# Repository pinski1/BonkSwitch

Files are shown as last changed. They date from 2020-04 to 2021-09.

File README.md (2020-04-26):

# BonkSwitch
For the remote control of 2 solenoids.

<!-- 3D image of the board here -->

## Specification

* Will accept +30V (8s) to +52 (12s) input voltages on an XT60 connector
* Will drive 2 solenoids with +24V at 60W each via XT30 connectors.
* Has an on board [FrSky XM](https://www.frsky-rc.com/product/xm-1g-sbus-non-telemetry/) reciever with 15 channels
* Will accept any [Adafruit Feather](https://learn.adafruit.com/adafruit-feather/feather-specification) compatible microcontroller board.
* Has voltage monitoring of all power rails and current monitoring of solenoids

While example code is provided it will require modification for your application & chosen Feather.

## Current status

Currently the PCB is in the final stages of review and should be finalised shortly.

The firmware efforts are still on going, although the majority of the work can only be completed once the hardware is available.

## Acknowledgements

* The team behind the robot [Nelly the Ellybot](https://www.facebook.com/teampunchant/)
* The team at [Bristol Bots](https://bristolbotbuilders.com/)
* My friend [Steve](https://twitter.com/BookSwapSteve) for the Feather outline

## Licence
Don't be a tit.
But see LICENCE for more details/legalese.

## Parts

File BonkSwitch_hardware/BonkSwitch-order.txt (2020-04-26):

Quantity	Value	Package	Order code	Manufacturer	Manuf. Code	Availability	Price (from)	Description
1	FEATHERWING_NODIM	FEATHERWING_DIM	unknown					
1	FRSKY_XM+	FRSKY_XM+	unknown					
10	100nF	C0603	unknown					
4	2.2uF 100V	C1210	2112727	TDK	C3225X7R2A225K230AB	10989	0.129	TDK - C3225X7R2A225K230AB - SMD Multilayer Ceramic Capacitor, 2.2 µF, 100 V, 1210 [3225 Metric], ± 10%, X7R, C Series TDK
4	10nF	C0603	unknown					
2	10uF 35V	C1210	2309017	TAIYO YUDEN	GMK325AB7106MM-T	1980	0.144	TAIYO YUDEN - GMK325AB7106MM-T - SMD Multilayer Ceramic Capacitor, 10 µF, 35 V, 1210 [3225 Metric], ± 20%, X7R, M Series
1	470pF	C0603	unknown					
1	100pF	C0603	unknown					
1	1uF	C0805	unknown					
1	47uF 100V	UD-10X10_NICHICON	1973389	PANASONIC	EEEHA2A470UP	1524	0.337	PANASONIC - EEEHA2A470UP - SMD Aluminium Electrolytic Capacitor, Radial Can - SMD, 47 µF, 100 V, HA Series, 1000 hours @ 105°C
1	120uF 35V	PANASONIC_E	2354806	PANASONIC	35SVPF120M	1	0.773	PANASONIC - 35SVPF120M - Polymer Aluminium Electrolytic Capacitor, 120 µF, 35 V, Radial Can - SMD, OS-CON SVPF Series
2	5.6V	SOD-323	unknown					
4	PMEG10030ELPX	SOD128	2498548	NEXPERIA	PMEG10030ELPX	52918	0.0919	NEXPERIA - PMEG10030ELPX - Schottky Rectifier, 100 V, 3 A, Single, SOD-128, 2 Pins, 770 mV
1	MBR130	SOD-123	2463407	ON SEMICONDUCTOR	MBR130LSFT1G	5080	0.0611	ON SEMICONDUCTOR - MBR130LSFT1G - Schottky Rectifier, 30 V, 1 A, Single, SOD-123FL, 2 Pins, 380 mV
1	LMR16030SDDAR	HSOIC8	2617078	TEXAS INSTRUMENTS	LMR16030SDDA .	637	1.96	TEXAS INSTRUMENTS - LMR16030SDDA . - DC/DC Switching Buck Regulator, Adjustable, 4.3V-60V in, 0.8V-50V out, 3A, HSOIC-8
1	LMR16006XDDC	SOT23-6	3007251	TEXAS INSTRUMENTS	LMR16006XDDCR	6791	1.13	TEXAS INSTRUMENTS - LMR16006XDDCR - DC-DC Switching Buck Step Down Regulator, Adjustable, 4V-60Vin, 2.1 MHz, 0.8V-55V/0.6Aout, SOT-6
1	FAN3227TMX	SOIC127P600X175-8N	2563218	ON SEMICONDUCTOR	FAN3227TMX	1885	0.437	ON SEMICONDUCTOR - FAN3227TMX - MOSFET Driver, 4.5V-18V supply, 3A output, SOIC-8
2	LMP8640MK-T	SOT23-6	3005385	TEXAS INSTRUMENTS	LMP8640MK-T/NOPB	0	0.676	TEXAS INSTRUMENTS - LMP8640MK-T/NOPB - Current Sense Amplifier, 1 Amplifier, 13 µA, TSOT-23, 6 Pins, -40 °C, 125 °C
1	74LVC1G14DBV	SOT23-5	1631687	NEXPERIA	74LVC1G14GW,125	14643	0.0387	NEXPERIA - 74LVC1G14GW,125 - Inverter, Schmitt Trigger, 74LVC1G14, 1 Input, 50 mA, 1.65 V to 5.5 V, TSSOP-5
1	7443551221	WE-HCI_1350/1365	2082647	WURTH ELEKTRONIK	7443551221	310	2.48	WURTH ELEKTRONIK - 7443551221 - Power Inductor (SMD), 22 µH, 6 A, Shielded, 6.5 A, WE-HCI Series, 13.2mm x 12.8mm x 6.2mm
1	7447714470	WE-PD_1030/1050	2082682	WURTH ELEKTRONIK	7447714470	1457	1.55	WURTH ELEKTRONIK - 7447714470 - Power Inductor (SMD), 47 µH, 2.2 A, Shielded, 2.5 A, WE-PD Series, 10mm x 10mm x 5mm
2	GREEN	LED-0603	unknown					
1	RED	LED-0603	unknown					
2	Yellow	LED-0603	unknown					
1	PCB_DP_RECTANGLE-100X62	DP10062_V1	unknown					
1	SI2302CDS	SOT23	1684049	VISHAY	SI2302CDS-T1-GE3	8121	0.13	VISHAY - SI2302CDS-T1-GE3 - Power MOSFET, N Channel, 20 V, 2.9 A, 0.045 ohm, TO-236, Surface Mount
4	2k2	R0603	unknown					
2	0R01	R2512	1435947	BOURNS	CRA2512-FZ-R010ELF	14930	0.208	BOURNS - CRA2512-FZ-R010ELF - SMD Current Sense Resistor, 0.01 ohm, CR Series, 2512 [6432 Metric], 3 W, ± 1%, Metal Film
2	10R	R0805	unknown					
2	39k	R0805	unknown					
1	82k	R0603	unknown					
2	470k	R0603	unknown					
1	33k	R0603	unknown					
1	30k	R0603	unknown					
1	4k3	R0603	unknown					
2	47k	R0603	unknown					
1	130k	R0603	unknown					
2	20k	R0603	unknown					
1	620k	R0603	unknown					
1	2k2	R0805	unknown					
1	56k	R0603	unknown					
1	68k	R0603	unknown					
1	11k	R0603	unknown					
4	100R	R0603	unknown					
5	10k	R0603	unknown					
4	SHORTT1	SHORT_TOP-01	unknown					
2	IRF7493TRPBF	SO-08	2725911	INFINEON	IRF7493TRPBF	4215	0.42	INFINEON - IRF7493TRPBF - Power MOSFET, N Channel, 80 V, 9.3 A, 0.0115 ohm, SOIC, Surface Mount
3	TESTPOINT_1.5X1.5	TESTPAD_1.5X1.5	unknown					
1	XT60PW-M	XT60PW-M	unknown					
2	XT30PW-F	XT30PW-F	unknown

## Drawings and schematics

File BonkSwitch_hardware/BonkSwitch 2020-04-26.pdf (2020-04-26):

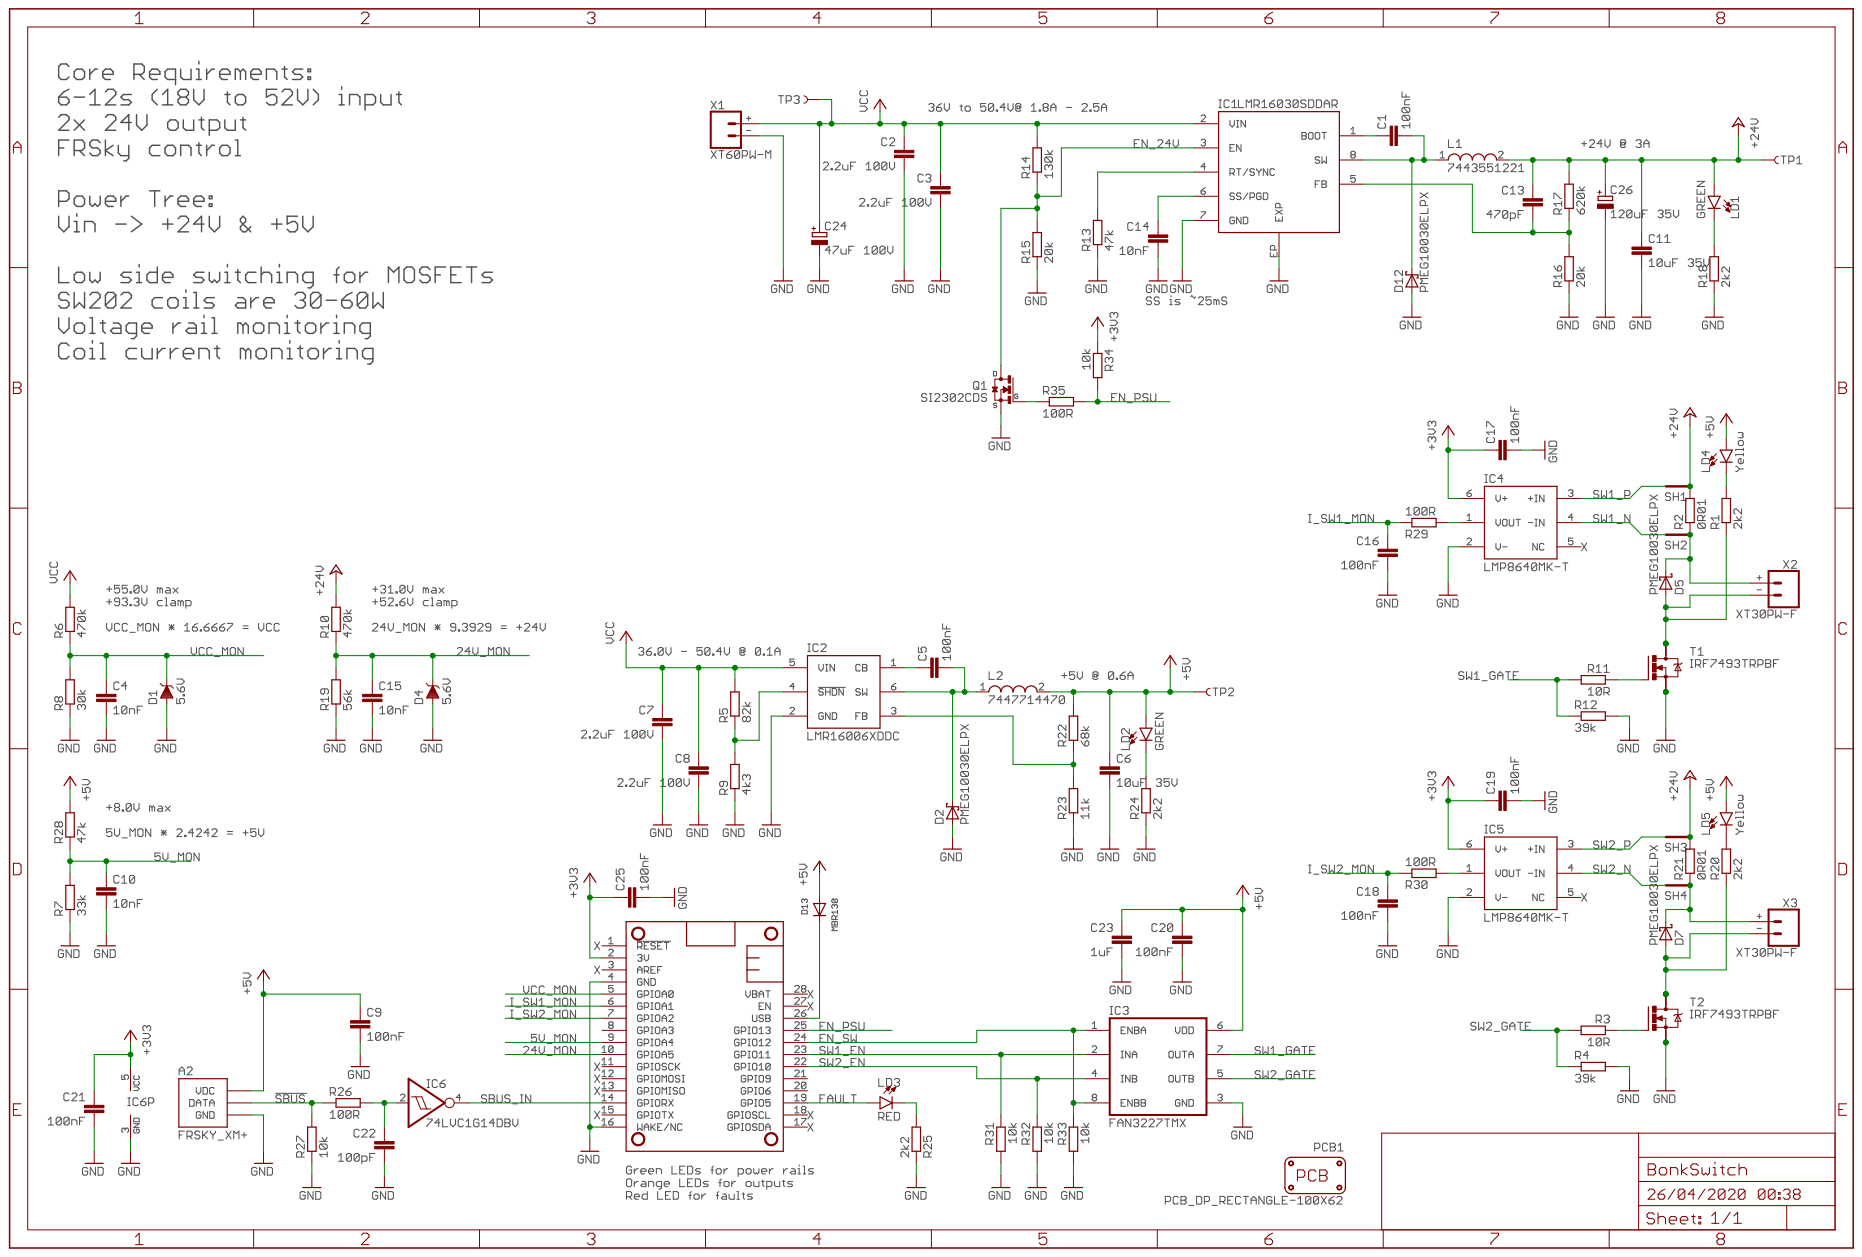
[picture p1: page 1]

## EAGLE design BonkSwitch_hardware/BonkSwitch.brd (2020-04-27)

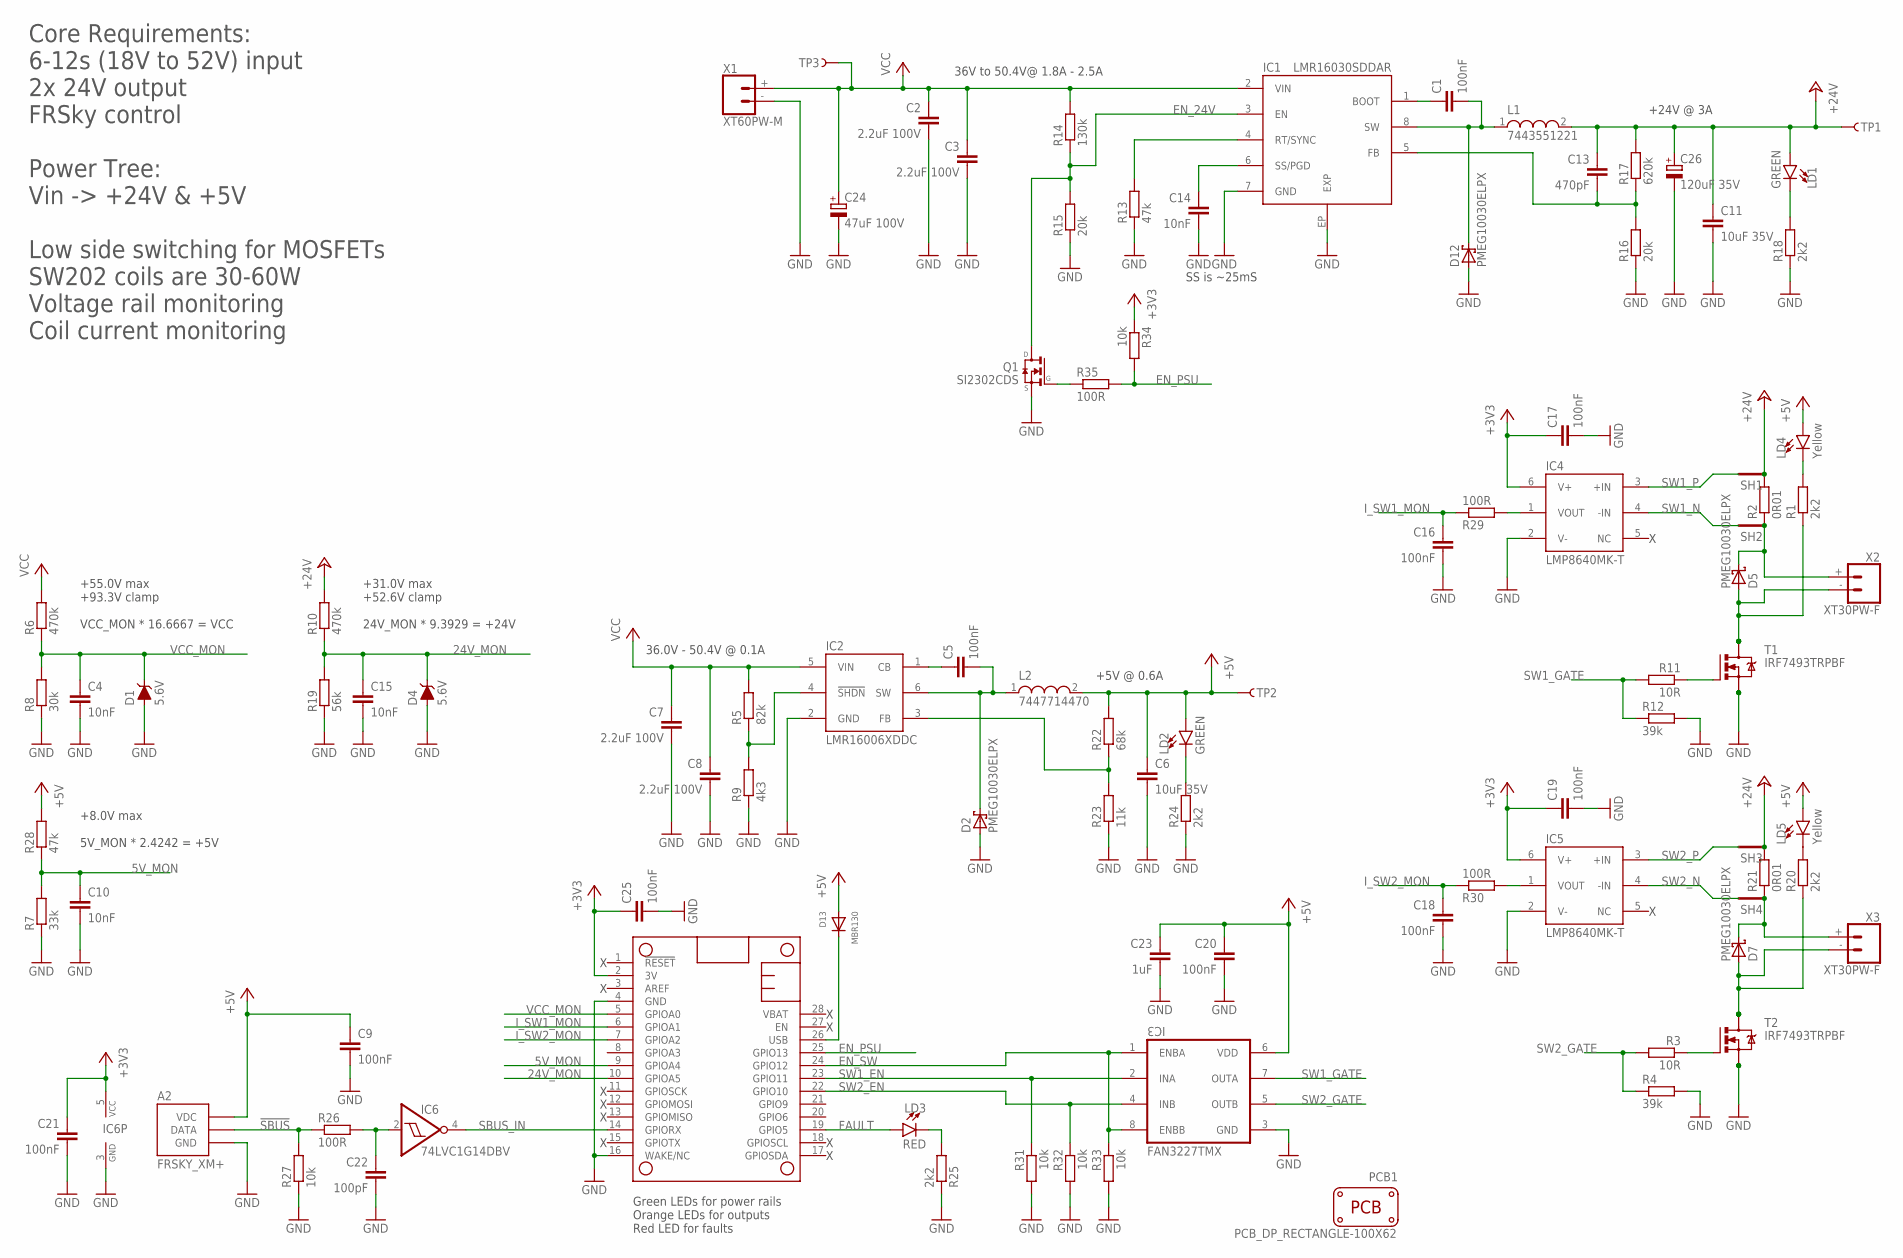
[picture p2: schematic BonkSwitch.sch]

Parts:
A1: FEATHERWING_NODIM; FEATHERWING_DIM
A2: FRSKY_XM+
C1, C5, C9, C16, C17, C18, C19, C20, C21, C25: 100nF; C0603
C2, C3, C7, C8: 2.2uF 100V; C1210; MPN C3225X7R2A225K230AB
C4, C10, C14, C15: 10nF; C0603
C6, C11: 10uF 35V; C1210; MPN GMK325AB7106MM-T
C13: 470pF; C0603
C22: 100pF; C0603
C23: 1uF; C0805
C24: 47uF 100V; UD-10X10_NICHICON; MPN EEEHA2A470UP
C26: 120uF 35V; PANASONIC_E; MPN 35SVPF120M
D1, D4: 5.6V; SOD-323; MPN MM3Z4V3ST1G
D2, D5, D7, D12: PMEG10030ELPX; SOD128; MPN PMEG10030ELPX
D13: MBR130; SOD-123; MPN MBR130LSFT1G
IC1: LMR16030SDDAR; HSOIC8; MPN LMR16030SDDA .
IC2: LMR16006XDDC; SOT23-6; MPN LMR16006XDDCR
IC3: FAN3227TMX; SOIC127P600X175-8N; MPN FAN3227TMX
IC4, IC5: LMP8640MK-T; SOT23-6; MPN LMP8640MK-T/NOPB
IC6: 74LVC1G14DBV; SOT23-5; MPN 74LVC1G14GW,125
L1: 7443551221; WE-HCI_1350/1365; MPN 7443551221
L2: 7447714470; WE-PD_1030/1050; MPN 7447714470
LD1, LD2: GREEN; LED-0603
LD3: RED; LED-0603
LD4, LD5: Yellow; LED-0603
PCB1: PCB_DP_RECTANGLE-100X62; DP10062_V1
Q1: SI2302CDS; SOT23; MPN SI2302CDS-T1-GE3
R1, R20, R24, R25: 2k2; R0603
R2, R21: 0R01; R2512; MPN CRA2512-FZ-R010ELF
R3, R11: 10R; R0805
R4, R12: 39k; R0805
R5: 82k; R0603
R6, R10: 470k; R0603
R7: 33k; R0603
R8: 30k; R0603
R9: 4k3; R0603
R13, R28: 47k; R0603
R14: 130k; R0603
R15, R16: 20k; R0603
R17: 620k; R0603
R18: 2k2; R0805
R19: 56k; R0603
R22: 68k; R0603
R23: 11k; R0603
R26, R29, R30, R35: 100R; R0603
R27, R31, R32, R33, R34: 10k; R0603
SH1, SH2, SH3, SH4: SHORTT1; SHORT_TOP-01
T1, T2: IRF7493TRPBF; SO-08; MPN IRF7493TRPBF
TP1, TP2, TP3: TESTPOINT_1.5X1.5; TESTPAD_1.5X1.5
X1: XT60PW-M
X2, X3: XT30PW-F

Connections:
5V_MON: A1.9 (GPIOA4), C10.1, R7.2, R28.1
24V_MON: A1.10 (GPIOA5), C15.1, D4.C, R10.1, R19.2
!SBUS: A2.3 (DATA), R26.1, R27.2
!SBUS_FILT: C22.1, IC6.2 (I), R26.2
+3V3: A1.2 (3V), C17.1, C19.1, C21.1, C25.1, IC4.6 (V+), IC5.6 (V+), IC6.5 (VCC), R34.1
+5V: A2.2 (VDC), C6.1, C9.1, C20.1, C23.1, D13.A, IC3.6 (VDD), L2.2, LD2.A, LD4.A, LD5.A, R22.2, R28.2, TP2.1
+24V: C11.1, C13.1, C26.+, L1.2, LD1.A, R2.2, R10.2, R17.2, R21.2, SH1.1, SH3.1, TP1.1
BST_5V: C5.1, IC2.1 (CB)
BST_24V: C1.1, IC1.1 (BOOT)
EN_5V: IC2.4 (!SHDN!), R5.1, R9.2
EN_24V: IC1.3 (EN), Q1.3 (D), R14.1, R15.2
EN_PSU: A1.25 (GPIO13), R34.2, R35.2
EN_SW: A1.24 (GPIO12), IC3.1 (ENBA), IC3.8 (ENBB), R33.1
FAULT: A1.19 (GPIO5), LD3.A
FB_5V: IC2.3 (FB), R22.1, R23.2
FB_24V: C13.2, IC1.5 (FB), R16.2, R17.1
GND: A1.4 (GND), A1.16 (WAKE/NC), A2.1 (GND), C2.2, C3.2, C4.2, C6.2, C7.2, C8.2, C9.2, C10.2, C11.2, C14.2, C15.2, C16.2, C17.2, C18.2, C19.2, C20.2, C21.2, C22.2, C23.2, C24.-, C25.2, C26.-, D1.A, D2.A, D4.A, D12.A, IC1.7 (GND), IC1.EP (EXP), IC2.2 (GND), IC3.3 (GND), IC4.2 (V-), IC5.2 (V-), IC6.3 (GND), Q1.2 (S), R4.2, R7.1, R8.1, R9.1, R12.2, R13.1, R15.1, R16.1, R18.1, R19.1, R23.1, R24.1, R25.1, R27.1, R31.2, R32.2, R33.2, T1.1 (S), T1.2 (S), T1.3 (S), T2.1 (S), T2.2 (S), T2.3 (S), X1.- (1)
I_SW1: IC4.1 (VOUT), R29.2
I_SW1_MON: A1.6 (GPIOA1), C16.1, R29.1
I_SW2: IC5.1 (VOUT), R30.2
I_SW2_MON: A1.7 (GPIOA2), C18.1, R30.1
unnamed: D7.C, R21.1, SH4.1, X3.+ (2)
unnamed: Q1.1 (G), R35.1
unnamed: R11.1, T1.4 (G)
unnamed: D5.A, R1.1, T1.5 (D), T1.6 (D), T1.7 (D), T1.8 (D), X2.- (1)
unnamed: LD4.C, R1.2
unnamed: R3.1, T2.4 (G)
unnamed: D7.A, R20.1, T2.5 (D), T2.6 (D), T2.7 (D), T2.8 (D), X3.- (1)
unnamed: LD5.C, R20.2
unnamed: D5.C, R2.1, SH2.1, X2.+ (2)
unnamed: LD3.C, R25.2
unnamed: LD1.C, R18.2
unnamed: LD2.C, R24.2
RT_24V: IC1.4 (RT/SYNC), R13.2
SBUS_IN: A1.14 (GPIORX), IC6.4 (O)
SS_24V: C14.1, IC1.6 (SS/PGD)
SW1_EN: A1.23 (GPIO11), IC3.2 (INA), R31.1
SW1_GATE: IC3.7 (OUTA), R11.2, R12.1
SW1_N: IC4.4 (-IN), SH2.2
SW1_P: IC4.3 (+IN), SH1.2
SW2_EN: A1.22 (GPIO10), IC3.4 (INB), R32.1
SW2_GATE: IC3.5 (OUTB), R3.2, R4.1
SW2_N: IC5.4 (-IN), SH4.2
SW2_P: IC5.3 (+IN), SH3.2
SW_5V: C5.2, D2.C, IC2.6 (SW), L2.1
SW_24V: C1.2, D12.C, IC1.8 (SW), L1.1
VCC: C2.1, C3.1, C7.1, C8.1, C24.+, IC1.2 (VIN), IC2.5 (VIN), R5.2, R6.2, R14.2, TP3.1, X1.+ (2)
VCC_MON: A1.5 (GPIOA0), C4.1, D1.C, R6.1, R8.2
V_USB: A1.26 (USB), D13.C

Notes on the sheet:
Core Requirements: 6-12s (18V to 52V) input 2x 24V output FRSky control Power Tree: Vin -> +24V & +5V Low side switching for MOSFETs SW202 coils are 30-60W Voltage rail monitoring Coil current monitoring
+55.0V max +93.3V clamp VCC_MON * 16.6667 = VCC
+31.0V max +52.6V clamp 24V_MON * 9.3929 = +24V
+24V @ 3A
36V to 50.4V@ 1.8A - 2.5A
+5V @ 0.6A
36.0V - 50.4V @ 0.1A
Green LEDs for power rails Orange LEDs for outputs Red LED for faults
SS is ~25mS
+8.0V max 5V_MON * 2.4242 = +5V

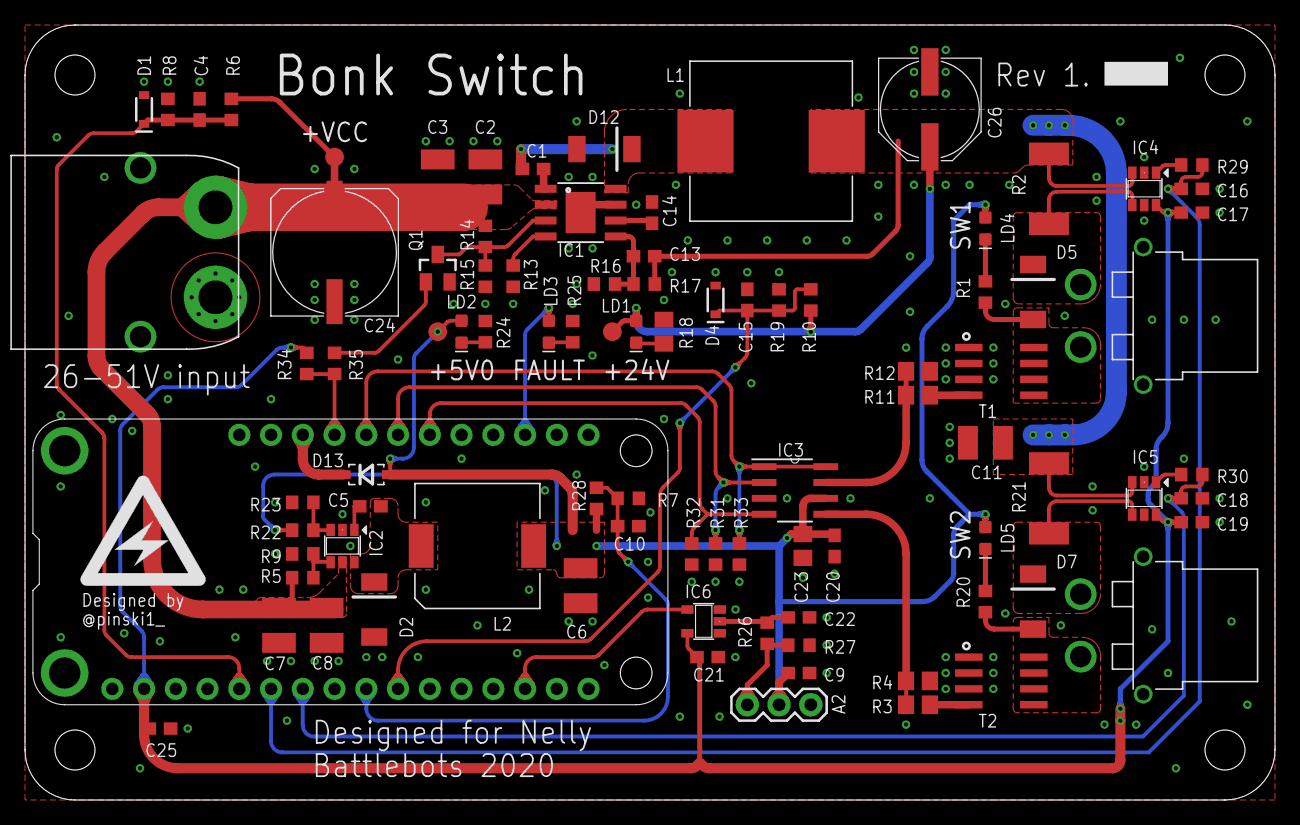
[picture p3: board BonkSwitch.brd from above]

Board: 2 copper layers, 100.0 x 62.0 mm, 97 parts (0 on the bottom side), 49 nets.

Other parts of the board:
LG1: LOGO_10X10

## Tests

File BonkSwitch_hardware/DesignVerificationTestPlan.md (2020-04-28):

# Bonk Switch - Design Verification Test Plan
Need to test the design to verify it meets the specification.

## Equipment Required

|Equipment|Model|Serial Number|
|---|-----|---|
|PSU, 60V 3A|||
|XT60 cable|||
|XT30 10Ω load|||
|Multi-meter|||
|Oscilloscope|||
|Oscilloscope probes|||
|USB Micro cable|||
|Thermal Camera|||

## Test Plan

|Test|Description|Criteria|Pass |Notes|
|----|---|---|-----|-----|
|Visually inspect the board|Is anything out of place?|Shorts|❌| |
|||Tombstoning|❌| |
|||PCB Faults|❌| |
|||Cold joints|❌| |
|||Serial Number present|❌| |
|Test for Shorts|Multi-meter on conitinuity mode||
|||OC between VCC (TP3) & GND|❌| |
|||OC between +24V (TP1) & GND|❌| |
|||OC between +5V (TP2) & GND|❌| |
|||OC between +3V3 (A1.p2) & GND|❌| |

Remove the Feather for the following tests.

Apply current limited +40V @ 3A power via the XT60.

|Test|Description|Criteria|Pass |Notes|
|----|---|---|-----|-----|
| | | |❌| |
|Measure the voltage|VCC (TP3) & GND |VCC ±5%|❌| |
||+5V (TP2) & GND|+4.75V & +5.25V|❌| |
||+24V (TP1) & GND|0V & +0.08V|❌| |
|Check LEDs|+5V LED (LD2)|lit|❌| |
||+24V LED (LD1)|unlit|❌| |
||Fault LED (LD3)|unlit|❌| |
||SW1 LED (LD4)|unlit|❌| |
||SW2 LED (LD5)|unlit|❌| |

Place a jumper between pin 25 and pin 4 on the Feather to enable the +24V SMPS.

|Test|Description|Criteria|Pass |Notes|
|----|---|---|-----|-----|
|Measure the voltage|+24V (TP1) & GND |+21.60V & +26.40V|❌| |
|Check LEDs|+24V LED (LD1)|lit|❌| |
|Check Board Temp|Use thermal camera|No hot spots|❌| |

Remove power to board and jumper wire.

Program Feather with bringup firmware.

Fit Feather to board.

Apply current limited +40V @ 3A power via the XT60.

|Test|Description|Criteria|Pass |Notes|
|----|---|---|-----|-----|
|Feather powered|Check LEDs on feather|lit|❌| |
|Feather communicating|Plug USB cable in|Characters on terminal|❌| |
|ADC reading correctly|VCC_MON|raw: xxxx to xxxx|❌| |
||+5V_MON|raw: xxxx to xxxx|❌| |
|Feather controls +24V|Enable +24V SMPS|TP1 +21.60V & +26.40V|❌| |
|Check LEDs|Fault LED (LD3)|lit|❌| |
|ADC reading correctly|+24V_MON|raw: xxx to xxx|❌| |

* MOSFET switch testing
   * check MOSFETs are driven on with minimal ringing
   * check MOSFET on resistance is reasonable
   * check SW1 is feather controlled
   * check SW2 is feather controlled
   * check against load of 10Ω
||I_SW1_MON|raw: 0 to xxxx|❌| |
||I_SW2_MON|raw: 0 to xxxx|❌| |

* FrSky RX testing
   * recieving FrSky packets
   * able to bind FrSky to RX
   * can see sticks moving
* confirm operation when VCC >50V and <35V

## Test Conclusion

1. Fault with design
   1. PCB mod
   2. PCB fix

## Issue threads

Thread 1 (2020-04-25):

Need to move +5V monitoring off of A9

pinski1, 2020-04-25:
A9 isn't compiling correctly in the Arduino IDE. The pin also shares a 100k to the on board battery connection so may be pulled to +4.2V by the Lithium battery charger.

This will also allow the potential divider to be set to something a little more reasonable than 2x 100kΩ resistors. Use [this](http://www.ti.com/download/kbase/volt/volt_div3.htm) to calculate the new resistor values. Bonus points if it's an integer conversion factor.

pinski1, 2020-04-25:
Moved to A4.
Resistor divider made up of 47kΩ and 33kΩ.
Fixed in commit fd1ea05e47847317a846a86c4f4bd8a77284a996

Closed 2020-04-25.

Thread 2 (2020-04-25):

Missing a Bill of Materials

pinski1, 2020-04-25:
A basic BoM needs to be generated and uploaded.

pinski1, 2020-04-26:
Added in f1a38f9bac2f6656c8cff0e34b6bc3c29929b90a

Closed 2020-04-26.

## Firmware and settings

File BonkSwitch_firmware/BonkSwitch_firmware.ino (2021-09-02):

/** BonkSwitch
 *
 * See https://www.ti.com/tool/TIDA-00289
 *
 *
 * Written for the [Adafruit Feather M0 Basic Proto](https://www.adafruit.com/product/2772)
 * Using https://github.com/bolderflight/SBUS
 */
#include <elapsedMillis.h>
#include <SBUS.h>

/** Settings **/
const unsigned int loop_duration_us = 10000; // 100Hz → 10ms
// forward duration
// return duration
// RC channel settings


/** Pin Map **/
#define PIN_VCC_MON       (A0)
#define PIN_24V_MON       (A5)
#define PIN_5V_MON        (A4)
#define PIN_I_SW1_MON     (A1)
#define PIN_I_SW2_MON     (A2)
#define PIN_EN_PSU        (13)  // active low
#define PIN_EN_SW         (12)
#define PIN_SW1_EN        (11)
#define PIN_SW2_EN        (10)
#define PIN_FAULT         (5)
#define PIN_SBUS_IN       (0)

/** Prototypes **/
unsigned int convert_ADC(int channel);
SBUS rc_rx(Serial1);
elapsedMicros loop_elapsed_us;

/** Globals **/
enum _states {s_Failsafe, s_Idle, s_Firing, s_Returning} current_state;
volatile unsigned int counter_packet_missed = 0x00;
bool flag_packet_rdy;
uint16_t channels[16];
bool failSafe;
bool lostFrame;
unsigned int mon_vcc;
unsigned int mon_24v;
unsigned int mon_5v;
unsigned int mon_sw1;
unsigned int mon_sw2;
unsigned int eqv_12v;
unsigned int coil_current[2][20];
unsigned int coil_curr_index = 0;
String debug_buffer;


void setup(void) {

  pinMode(PIN_VCC_MON, INPUT);
  pinMode(PIN_24V_MON, INPUT);
  pinMode(PIN_5V_MON, INPUT);
  pinMode(PIN_I_SW1_MON, INPUT);
  pinMode(PIN_I_SW2_MON, INPUT);
  pinMode(PIN_EN_PSU, OUTPUT);
  pinMode(PIN_EN_SW, OUTPUT);
  pinMode(PIN_SW1_EN, OUTPUT);
  pinMode(PIN_SW2_EN, OUTPUT);
  pinMode(PIN_FAULT, OUTPUT);

  digitalWrite(PIN_EN_PSU, HIGH);
  digitalWrite(PIN_EN_SW, HIGH);
  digitalWrite(PIN_SW1_EN, LOW);
  digitalWrite(PIN_SW2_EN, LOW);
  digitalWrite(PIN_FAULT, HIGH);

  for (int i = 0; i < 20; i++)
  {
    coil_current[0][i] = 0x00;
    coil_current[1][i] = 0x00;
  }

  // USB UART debug setup
  Serial.begin(115200);
  Serial.println("BonkSwitch!");
  debug_buffer.reserve(128);
  while (Serial.available()) Serial.read();

  // SBus setup
  rc_rx.begin();

  // State Machine setup
  current_state = s_Failsafe;

  // finished setup
  digitalWrite(PIN_FAULT, LOW);
}

void loop(void) {

  if (loop_elapsed_us > loop_duration_us)
  {
    loop_elapsed_us -= loop_duration_us;

    // get voltage rails values
    mon_vcc = convert_ADC(PIN_VCC_MON);
    mon_24v = convert_ADC(PIN_24V_MON);
    mon_5v = convert_ADC(PIN_5V_MON);

    // calculate 12V equivalent
    eqv_12v = ((12000 * 256) / mon_24v);

    // get latest coil currents
    mon_sw1 = convert_ADC(PIN_I_SW1_MON);
    coil_current[0][coil_curr_index] = mon_sw1;
    mon_sw2 = convert_ADC(PIN_I_SW2_MON);
    coil_current[1][coil_curr_index] = mon_sw2;
    if (coil_curr_index == 19) coil_curr_index = 0;
    else coil_curr_index += 1;
    // over current protection?
    // solenoid armature position estimation

    // get latest RC packet
    flag_packet_rdy = rc_rx.read(&channels[0], &failSafe, &lostFrame);
    if(flag_packet_rdy == true) counter_packet_missed = 0x00;
    else if(counter_packet_missed < 20) counter_packet_missed ++;
    
    // get Serial commands
    for (int i = 0; i < 65; i++)
    {
      if (Serial.available() > 0) debug_buffer += char(Serial.read());
      else break;
    }
    if (debug_buffer.indexOf('\r') > 0)
    {
      if (debug_buffer.substring(0, debug_buffer.indexOf('\r')) == "STATUS")
      {
        Serial.println("BonkSwitch Status:");
        Serial.print("VCC is: "); Serial.print(mon_vcc / 1000, DEC); Serial.print('.'); Serial.print(mon_vcc % 1000, DEC); Serial.print("V\r\n");
        Serial.print("+24V is: "); Serial.print(mon_24v / 1000, DEC); Serial.print('.'); Serial.print(mon_24v % 1000, DEC); Serial.print("V\r\n");
        Serial.print("+5V is: "); Serial.print(mon_5v / 1000, DEC); Serial.print('.'); Serial.print(mon_5v % 1000, DEC); Serial.print("V\r\n");
        Serial.print("SW1 current is: "); Serial.print(mon_sw1, DEC); Serial.print("mA\r\n");
        Serial.print("SW2 current is: "); Serial.print(mon_sw2, DEC); Serial.print("mA\r\n");
        switch (current_state)
        {
          case s_Idle:
            Serial.println("Current state is: Idle");
            break;
          case s_Firing:
            Serial.println("Current state is: Firing");
            break;
          case s_Returning:
            Serial.println("Current state is: Returning");
            break;
          case s_Failsafe:
          default:
            Serial.println("Current state is: Failsafe!");
        }
        // SBUS status?
        //Serial.print(""); 
        Serial.print("The +24V PSU is "); Serial.println(!digitalRead(PIN_EN_PSU) ? "enabled" : "disabled");
        Serial.print("The switches are "); Serial.println(digitalRead(PIN_EN_SW) ? "enabled" : "disabled");
        Serial.print("Switch 1 is "); Serial.println(digitalRead(PIN_SW1_EN) ? "enabled" : "disabled");
        Serial.print("Switch 2 is "); Serial.println(digitalRead(PIN_SW2_EN) ? "enabled" : "disabled");
        Serial.print("There is "); Serial.println(digitalRead(PIN_FAULT) ? "a fault!" : "not a fault");
      }
      else if (debug_buffer.substring(0, debug_buffer.indexOf('\r')) == "PSU EN")
      {
        Serial.println("Enabling +24V PSU");
        digitalWrite(PIN_EN_PSU, LOW);
      }
      else if (debug_buffer.substring(0, debug_buffer.indexOf('\r')) == "PSU DIS")
      {
        Serial.println("Disabling +24V PSU");
        digitalWrite(PIN_EN_PSU, HIGH);
      }
      else if (debug_buffer.substring(0, debug_buffer.indexOf('\r')) == "SW1 EN")
      {
        Serial.println("Enabling SW1");
        digitalWrite(PIN_SW1_EN, HIGH);
      }
      else if (debug_buffer.substring(0, debug_buffer.indexOf('\r')) == "SW1 DIS")
      {
        Serial.println("Disabling SW1");
        digitalWrite(PIN_SW1_EN, LOW);
      }
      else if (debug_buffer.substring(0, debug_buffer.indexOf('\r')) == "SW2 EN")
      {
        Serial.println("Enabling SW2");
        digitalWrite(PIN_SW2_EN, HIGH);
      }
      else if (debug_buffer.substring(0, debug_buffer.indexOf('\r')) == "SW2 DIS")
      {
        Serial.println("Disabling SW2");
        digitalWrite(PIN_SW2_EN, LOW);
      }
      debug_buffer.remove(0);
    }

    /** weapon state machine **/
    switch (current_state)
    {
      case s_Idle:
        digitalWrite(PIN_EN_PSU, LOW);
        digitalWrite(PIN_FAULT, LOW);
        digitalWrite(PIN_SW1_EN, LOW); analogWrite(PIN_SW1_EN, 0);
        digitalWrite(PIN_SW2_EN, LOW); analogWrite(PIN_SW2_EN, 0);
        
        if(counter_packet_missed > 5 || channels[0] < 100) current_state = s_Failsafe;
        else if (channels[0] > 1500)  current_state = s_Firing;
        else if (channels[0] < 700)   current_state = s_Returning;
        break;
      case s_Firing:
        // enable firing solenoid
        digitalWrite(PIN_SW1_EN, HIGH);
        
        // ensure it doesn't over heat
        delay(3);
        analogWrite(PIN_SW1_EN, eqv_12v);
        
        if(counter_packet_missed > 5 || channels[0] < 100) current_state = s_Failsafe;
        else if (channels[0] > 700 && channels[0] < 1500)  current_state = s_Idle;
        break;
      case s_Returning:
        // enable retract solenoid
        digitalWrite(PIN_SW2_EN, HIGH);
        
        // ensure it doesn't over heat
        delay(3);
        analogWrite(PIN_SW2_EN, eqv_12v);
        
        if(counter_packet_missed > 5 || channels[0] < 100) current_state = s_Failsafe;
        else if (channels[0] > 700 && channels[0] < 1500)  current_state = s_Idle;
        break;
      case s_Failsafe:
      default:
        digitalWrite(PIN_FAULT, HIGH);
        digitalWrite(PIN_EN_PSU, HIGH);
        digitalWrite(PIN_SW1_EN, LOW);
        digitalWrite(PIN_SW2_EN, LOW);
        
        // monitor inputs for problems

        if(counter_packet_missed == 0) current_state = s_Idle;
    }

    if (loop_elapsed_us > loop_duration_us) Serial.println("Duration exceeded!");
  }

}

/**                                     Functions                                    **/


/** Returns the voltage/current measured on a pin in milliVolts/milliAmps.
    @param The pin to take the ADC reading from.
    @returns The value in milliVolts/milliAmps.
*/
inline unsigned int convert_ADC(int channel) {

  unsigned int adc_value = 0x00;
  const unsigned int _count = 0x04;
  const unsigned int _conv_vcc = 53711;  // (3.3V/1024)/(30kΩ/500kΩ)/1µV
  const unsigned int _conv_24v = 30270;  // (3.3V/1024)/(56kΩ/526kΩ)/1µV
  const unsigned int _conv_5v = 7813;    // (3.3V/1024)/(33kΩ/80kΩ)/1µV
  const unsigned int _conv_i_sw = 16113; // (3.3V/1024)/(20*0.01Ω)/1µV

  for (unsigned int i = 0; i < _count; i++) adc_value += analogRead(channel);
  adc_value /= _count;

  switch (channel) {
    case PIN_VCC_MON:
      adc_value *= _conv_vcc;
      break;
    case PIN_24V_MON:
      adc_value *= _conv_24v;
      break;
    case PIN_5V_MON:
      adc_value *= _conv_5v;
      break;
    case PIN_I_SW1_MON:
    case PIN_I_SW2_MON:
      adc_value *= _conv_i_sw;
      break;
    default:
      adc_value = 0xFFFFFFFF; // impossibly large number
  }
  return adc_value / 1000; // return milliVolts/milliAmps
}

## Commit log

2020-04-25 Initial commit
    Firmware is not complete.
    [BonkSwitch.brd, BonkSwitch.sch]
2020-04-25 Reorganising HW.
    [BonkSwitch.brd, BonkSwitch.sch]
2020-04-25 More directory reorg
    [BonkSwitch.brd, BonkSwitch.sch]
2020-04-25 Tuning Schematic.
    [BonkSwitch.brd, BonkSwitch.sch]
2020-04-25 Fixed SBUS bias resistor.
    [BonkSwitch.brd, BonkSwitch.sch]
2020-04-25 Moved +5V rail monitoring to A4
    [BonkSwitch.brd, BonkSwitch.sch]
2020-04-26 Updated schematic & BoM
    [BonkSwitch.brd, BonkSwitch.sch]
2020-04-27 Adding Zener part numbers
    [BonkSwitch.brd, BonkSwitch.sch]
2020-06-26 Adding switch control and SBUS decoding.
2021-09-02 Adding TI Current Controlled Driver for Solenoids app note

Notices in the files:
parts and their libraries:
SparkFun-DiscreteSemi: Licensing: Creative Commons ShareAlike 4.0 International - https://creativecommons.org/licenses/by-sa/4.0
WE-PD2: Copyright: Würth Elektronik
